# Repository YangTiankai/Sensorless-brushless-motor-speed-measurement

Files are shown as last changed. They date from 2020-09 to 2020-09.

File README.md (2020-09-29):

# Sensorless-brushless-motor-speed-measurement
使用电压比较器处理相电压的方法，测量四轴无人机无感无刷电机的转速，包含PCB和STM32源码，可以测量8路方波输入。输入端串联RC高通滤波器，可以处理有感无刷电机的霍尔传感器的转速反馈。

集成了力矩传感器的485通信模块和大疆N3飞控的通信模块。

使用了另一个项目的STM32F405核心板  
https://github.com/YangTiankai/STM32F4-Core-Board

# 系统结构

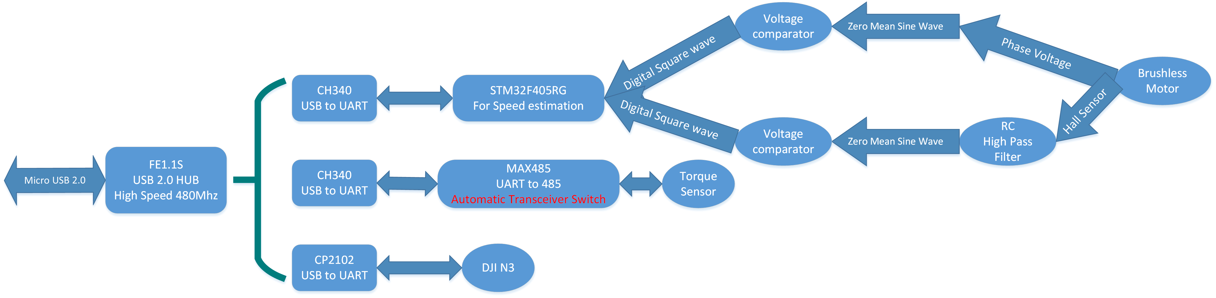
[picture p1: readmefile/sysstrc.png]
系统结构


# 测速原理
对于有12个线圈的无感电机，电机每转动一圈三相线上电压产生7个周期的正弦，将其输入电压比较器即可转化为数字方波，测量其频率可知转速。

对于有感电机，电机每转动一圈霍尔线上也是产生7个周期的正弦信号，但是该信号为恒正，使用一个10uF、10kΩ的RC高通滤波器去基频，即可得到零均正弦信号，输入电压比较器测量频率即可。

# 原理图和PCB

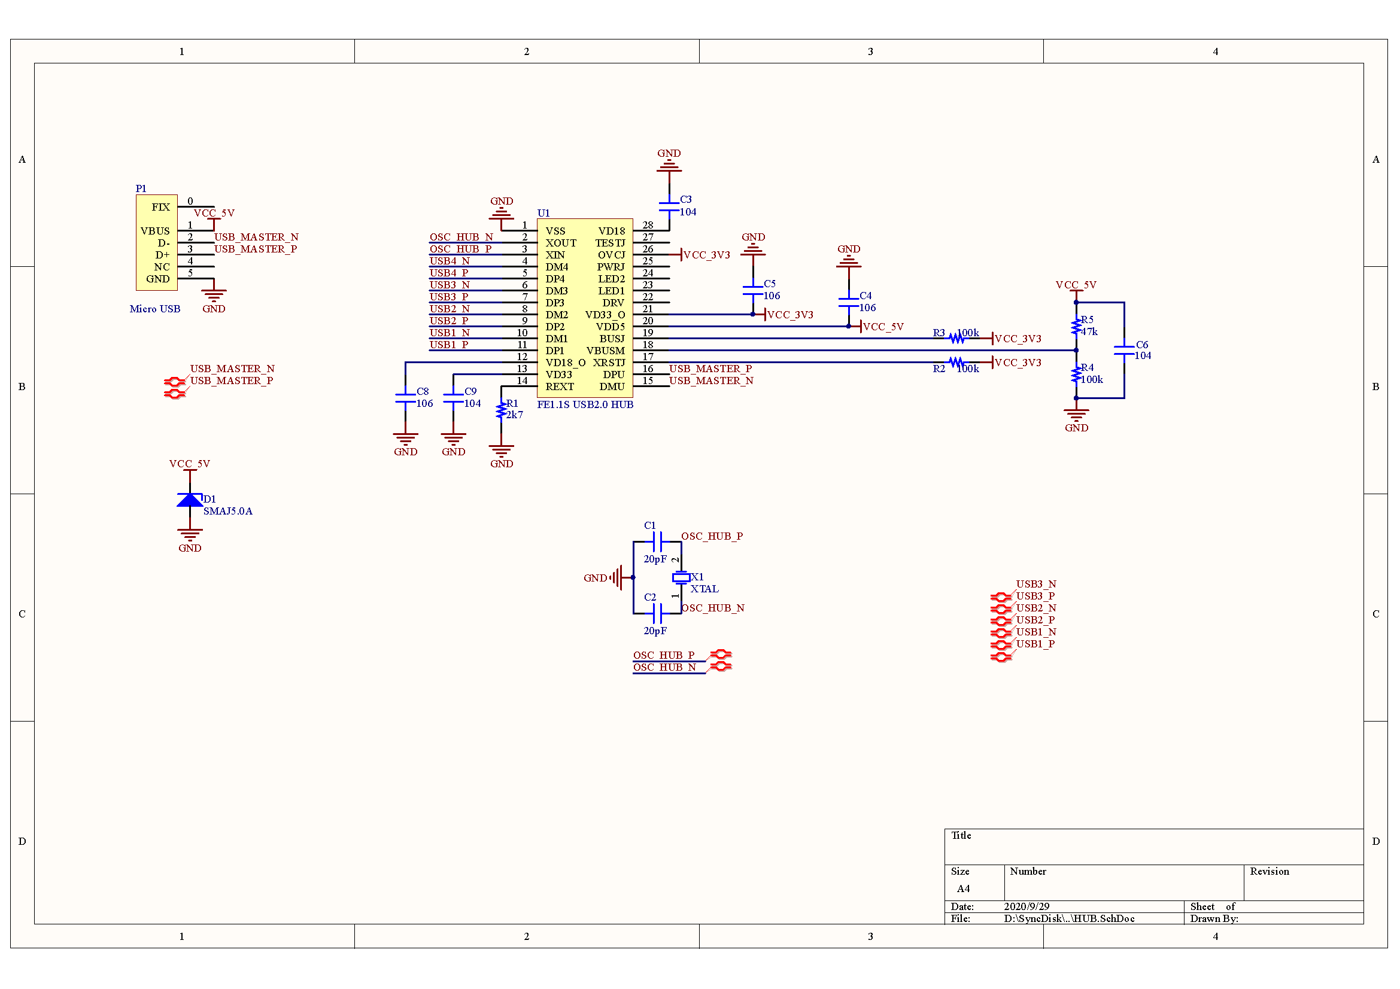
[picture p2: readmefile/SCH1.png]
SCH1


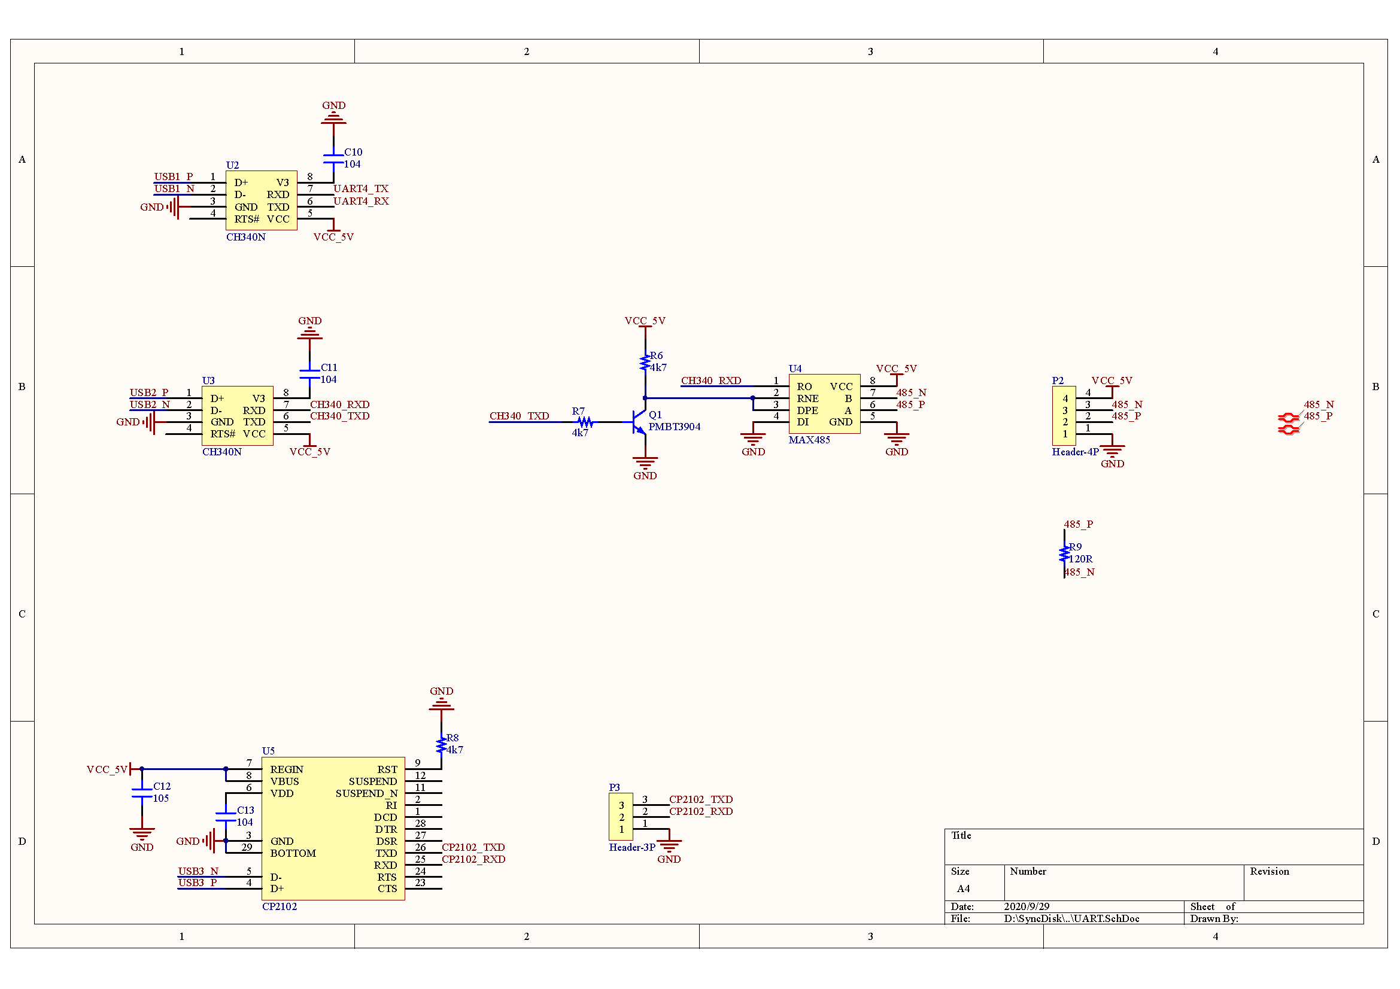
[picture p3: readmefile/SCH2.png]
SCH2


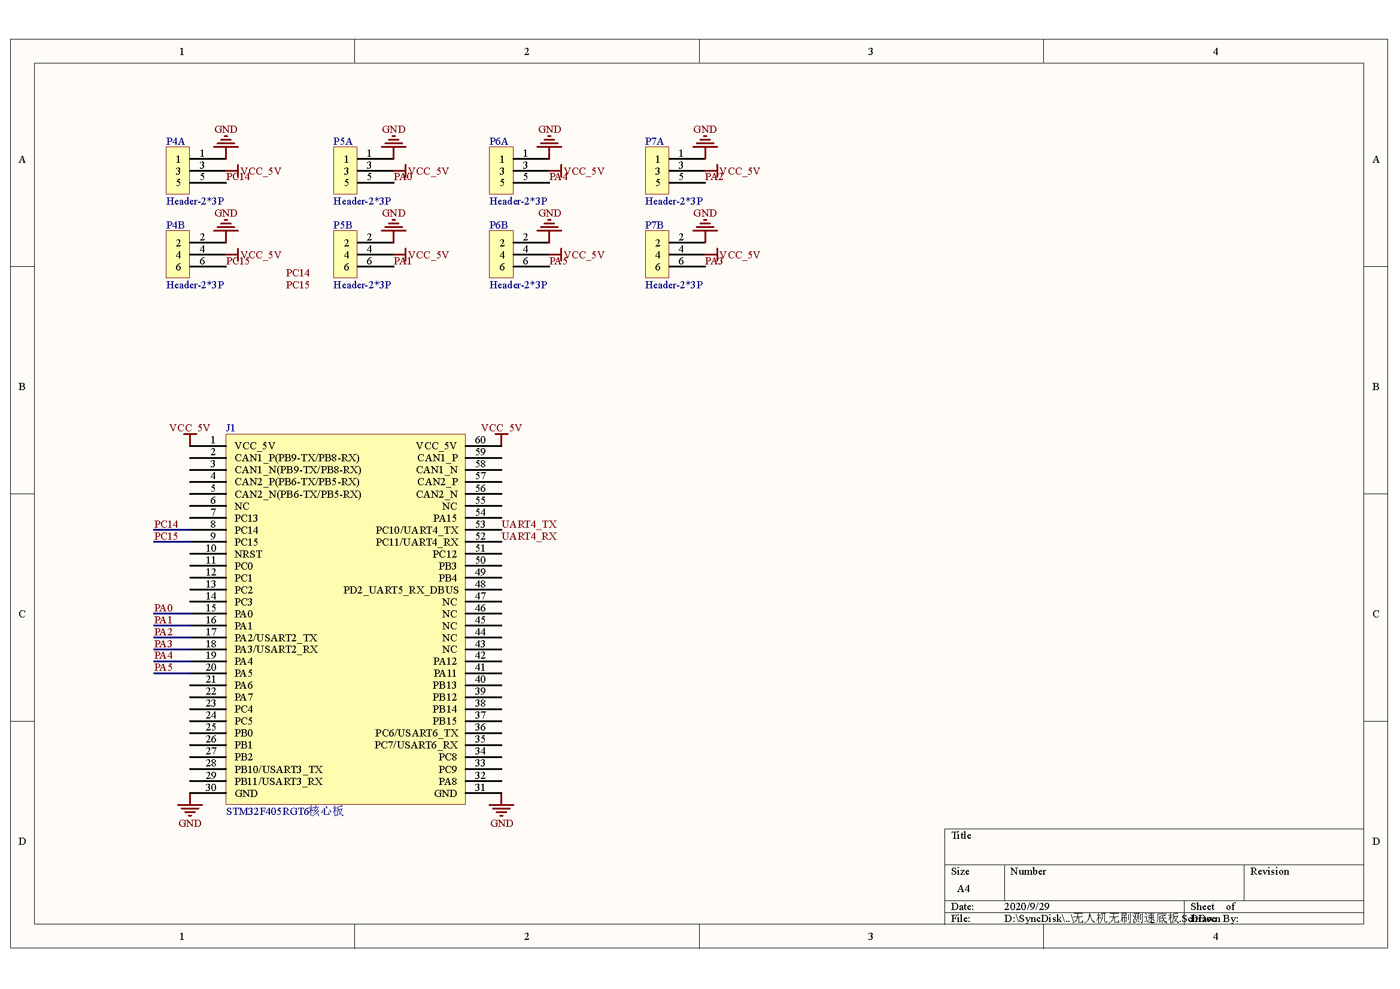
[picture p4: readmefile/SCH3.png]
SCH3


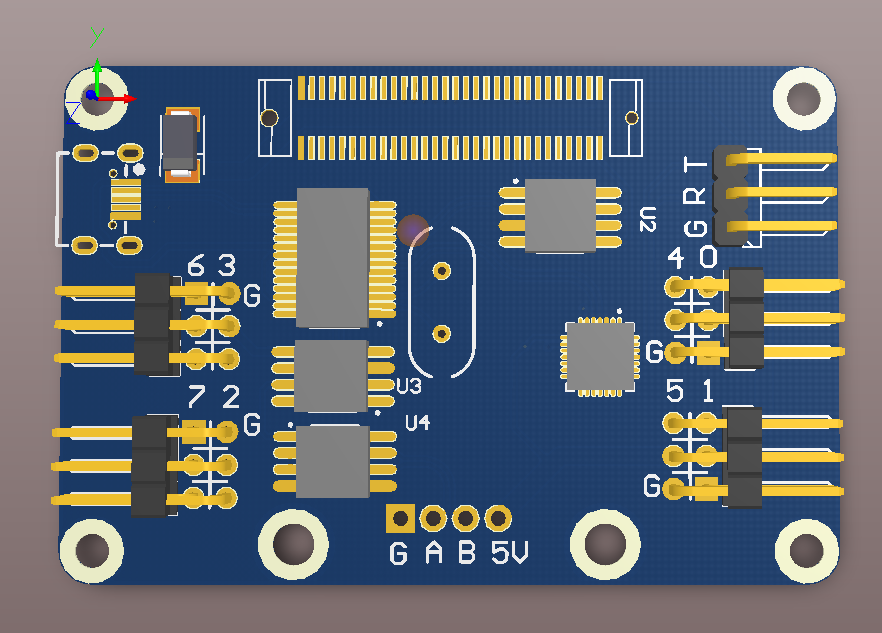
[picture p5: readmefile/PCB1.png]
PCB1


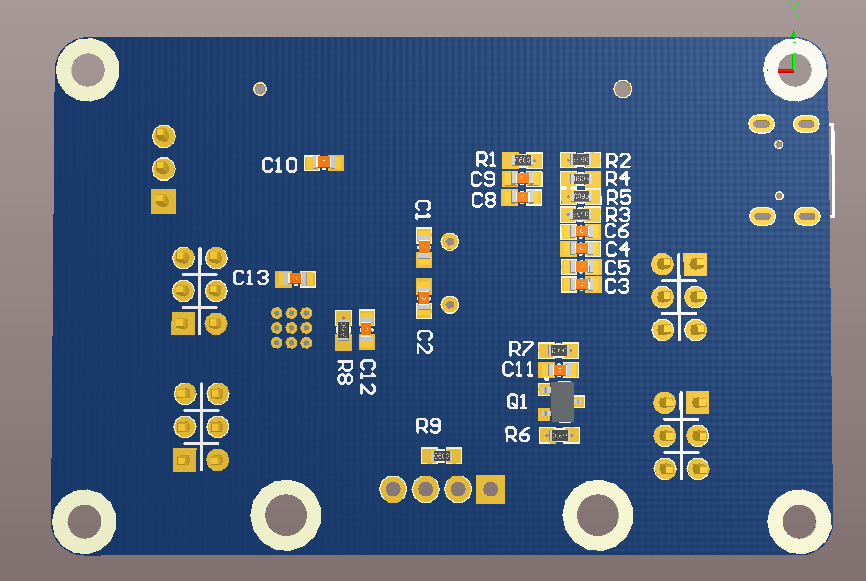
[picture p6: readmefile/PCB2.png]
PCB2


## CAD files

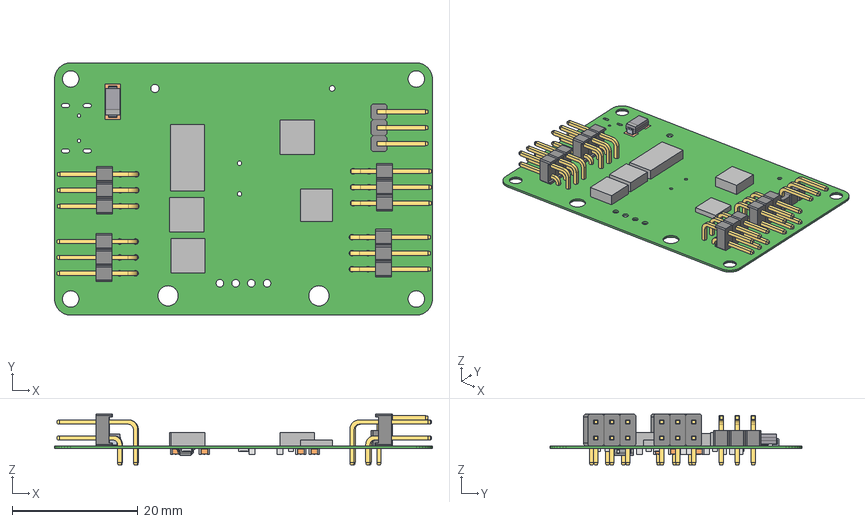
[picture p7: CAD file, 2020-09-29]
pcbfile/无人机无刷测速底板.step
60.2 x 40.2 x 8.10 mm
Board
R0603 x 9
User_Library-cap0603_cap0603_body_?? x 12
User_Library-cap0603_pad_0603_?? x 12
Extruded x 29
do214ac
do214acpad x 2
HDR-1x2_H x 12
LOGOԲ x 15
HDR2.54-1P_H x 3

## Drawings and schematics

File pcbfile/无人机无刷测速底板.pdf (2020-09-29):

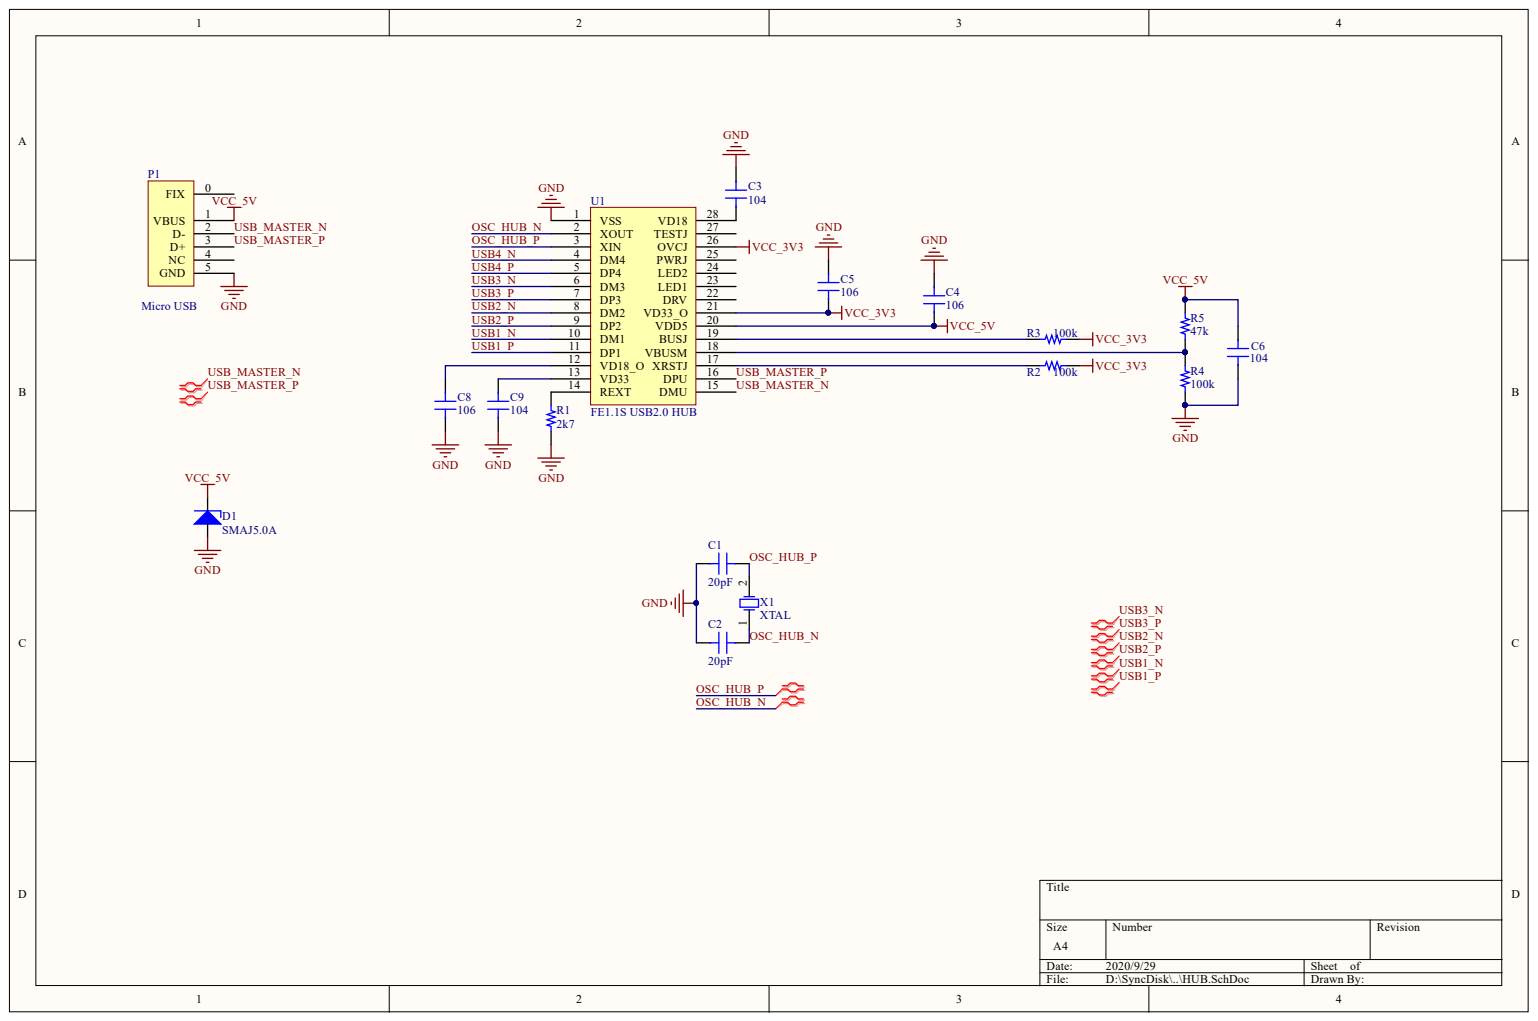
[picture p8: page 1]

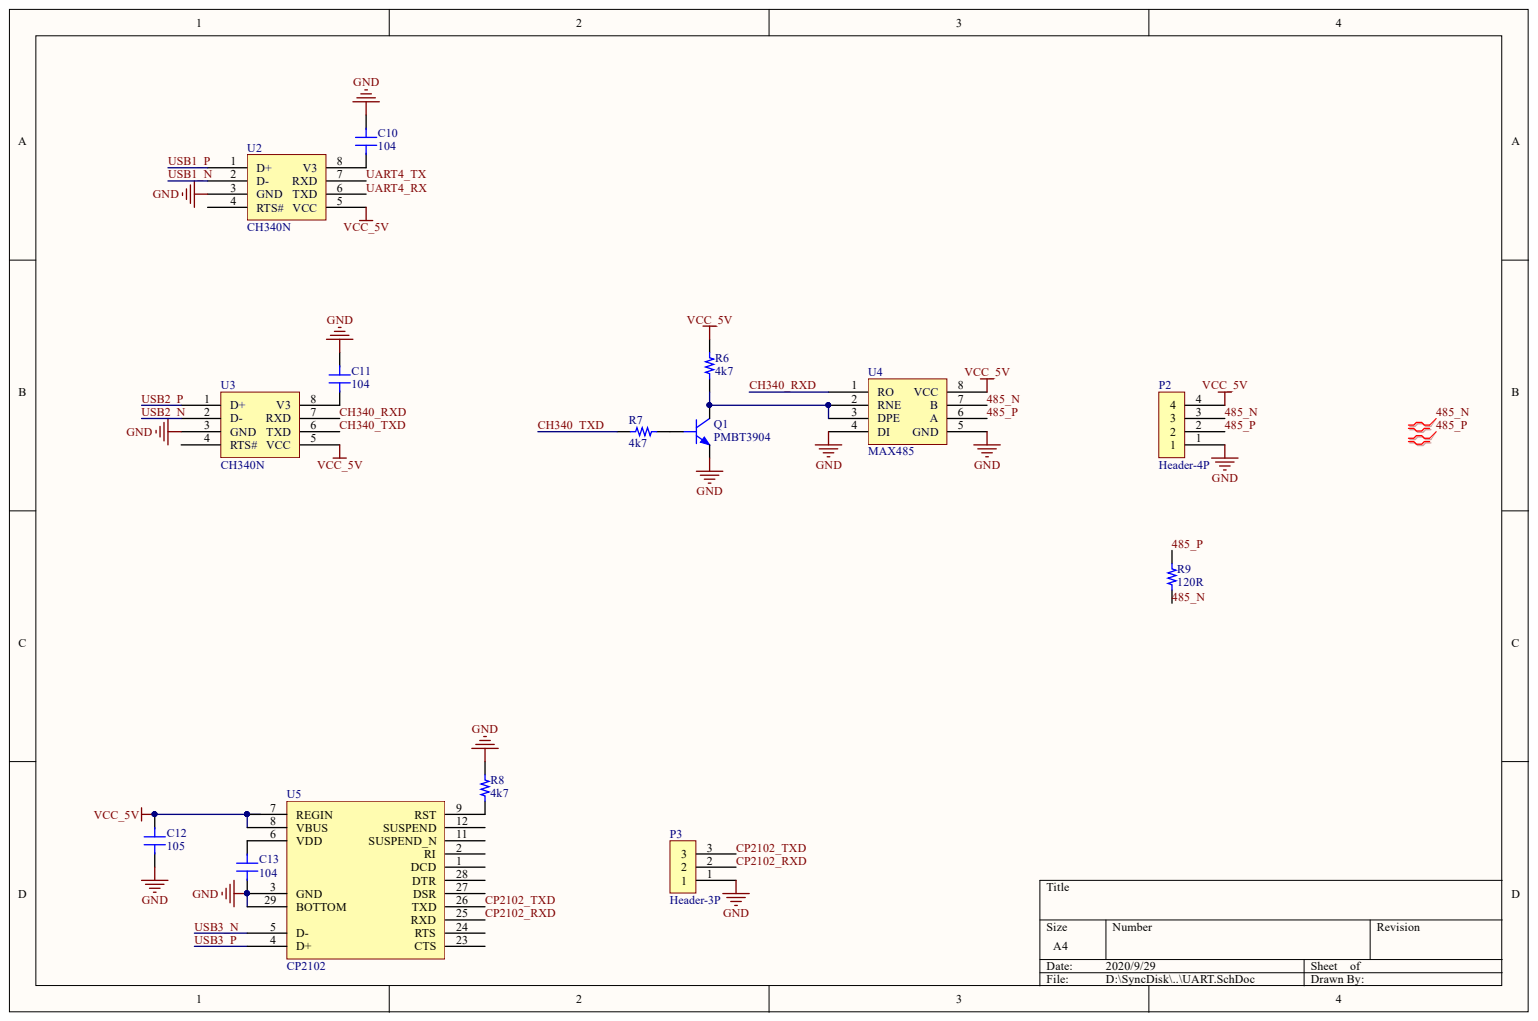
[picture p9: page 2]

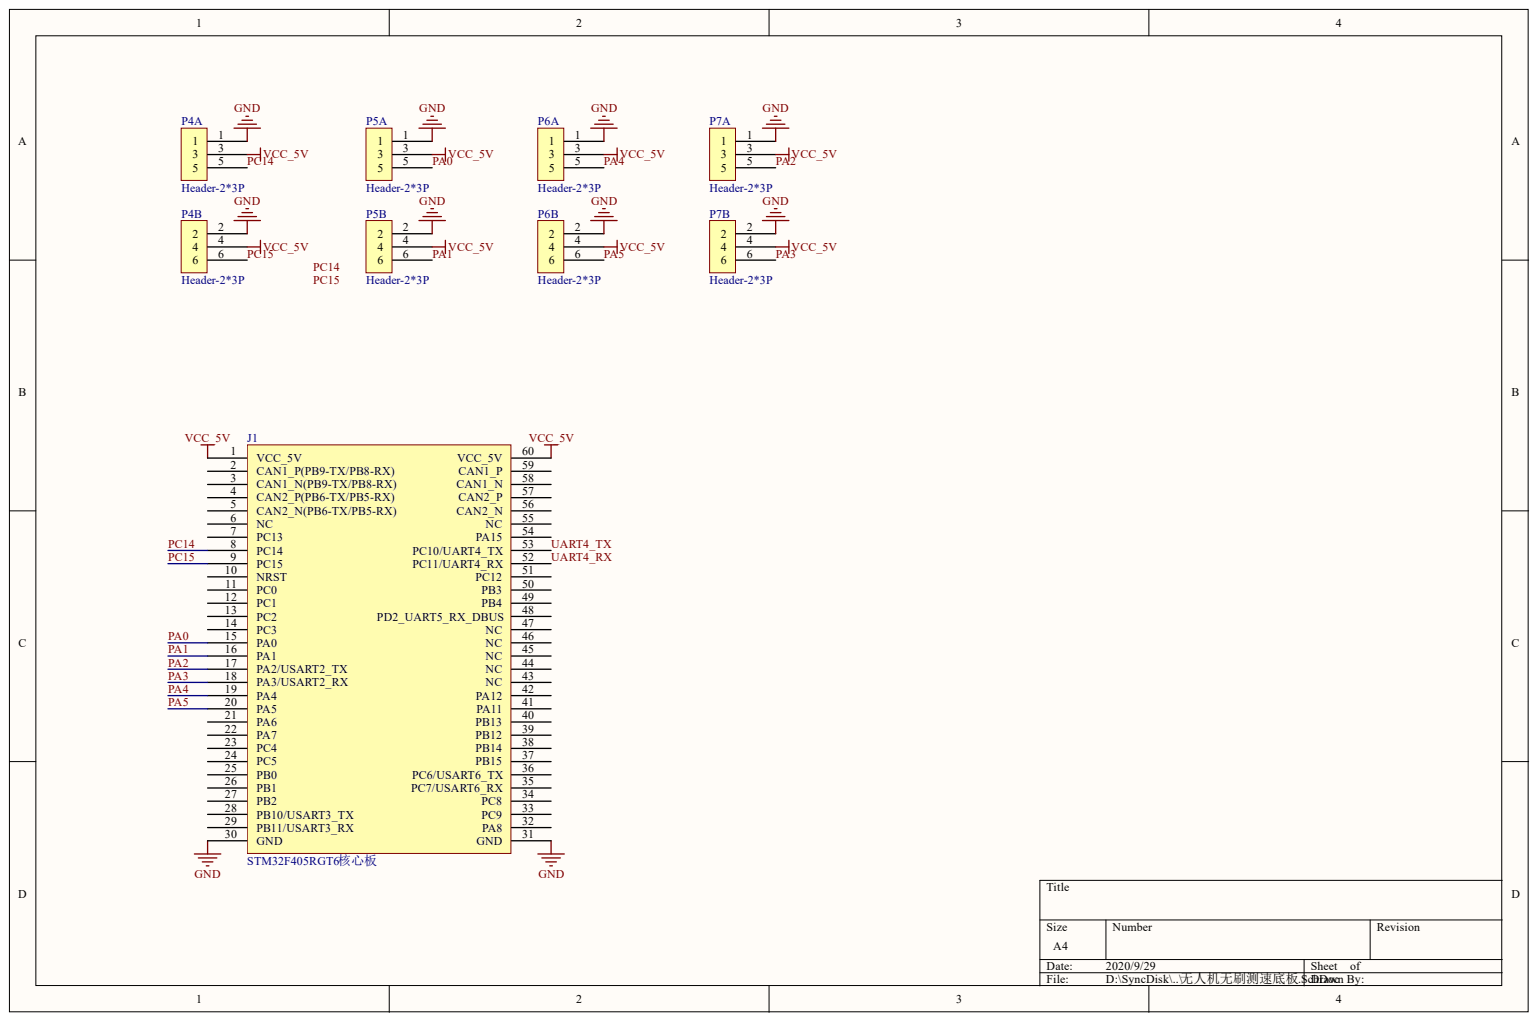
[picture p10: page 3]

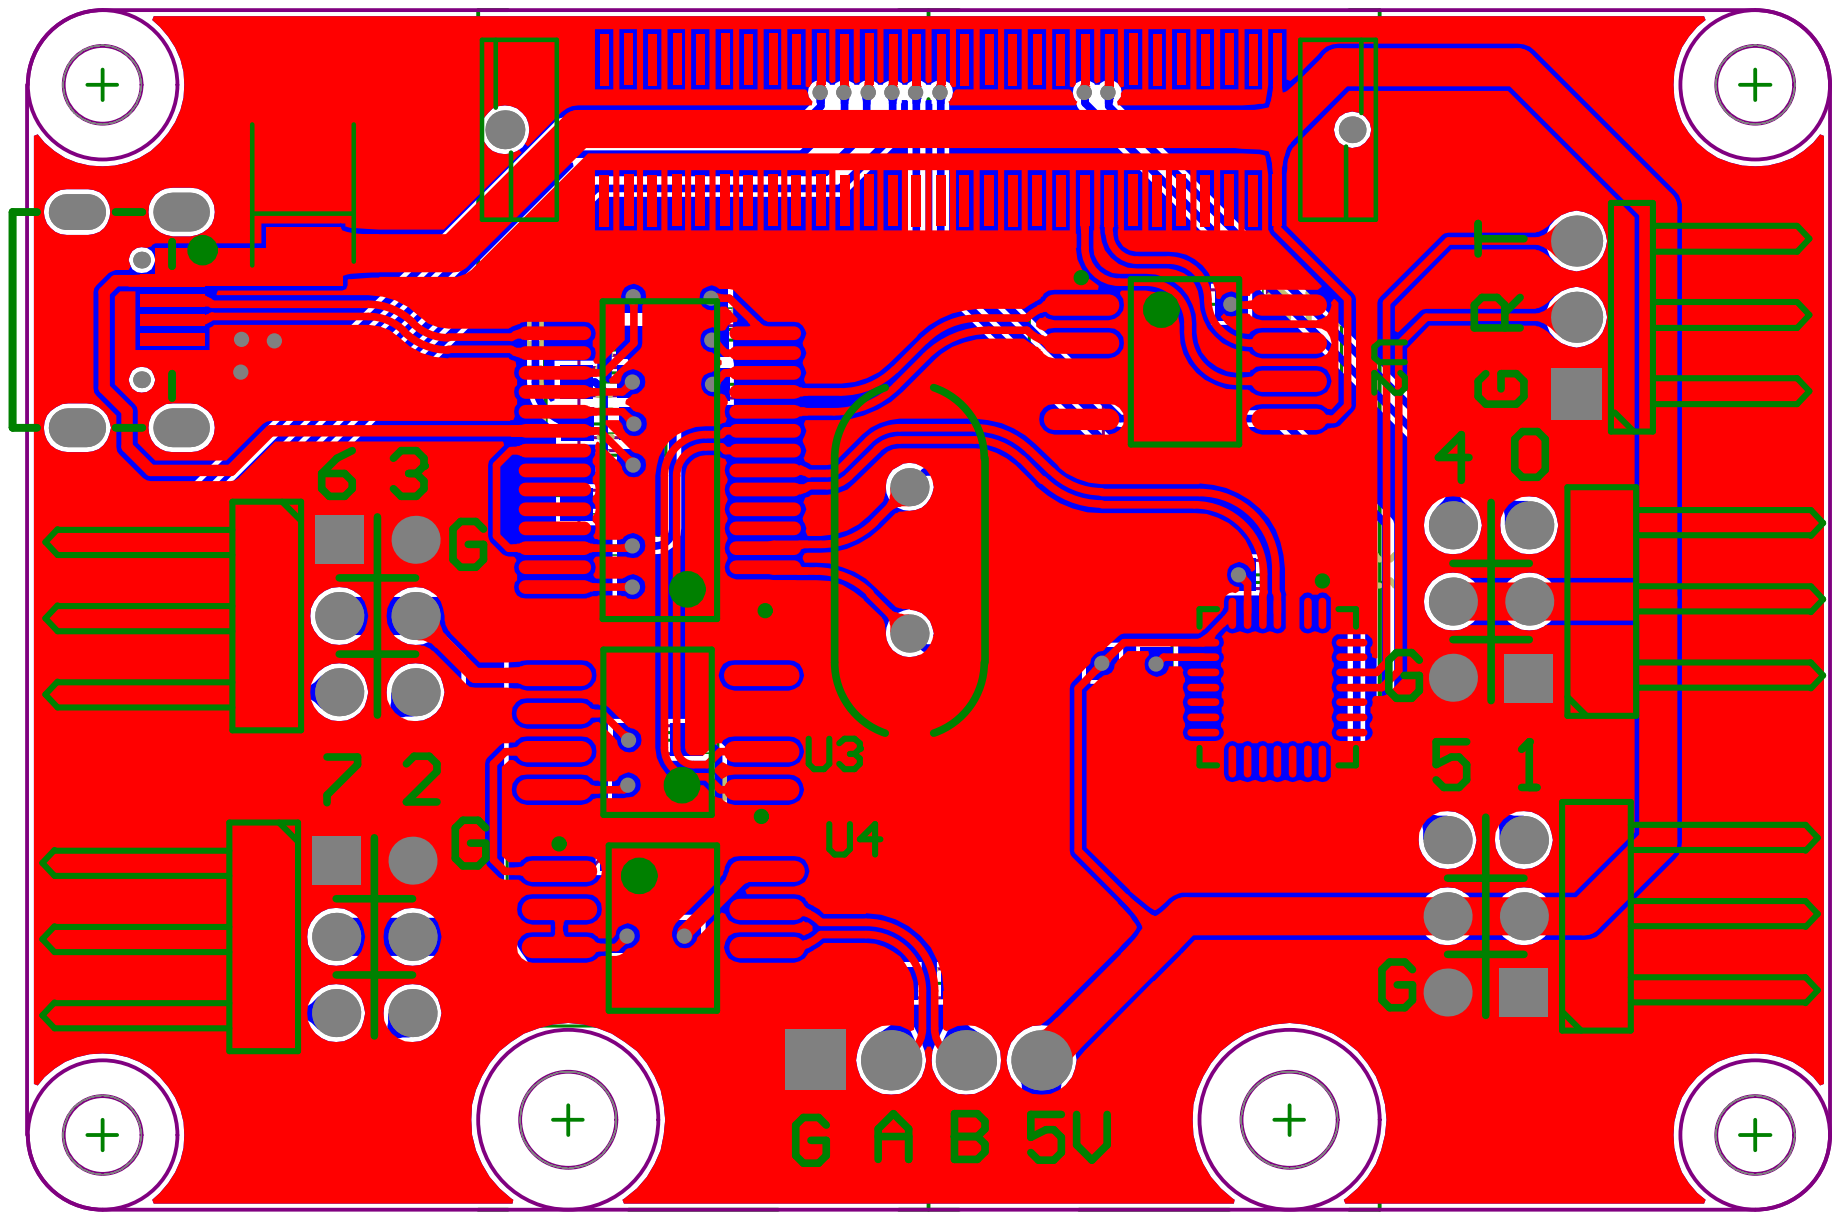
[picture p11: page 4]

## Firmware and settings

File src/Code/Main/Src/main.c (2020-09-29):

#include "main.h"
#include "math.h"



CLOCK clock = {0};
state_t state = {0};
uint8_t buff[256] = {0};
uint16_t len = 0;
uint8_t anobuff[256] = {0};
uint16_t anolen = 0;

time_stamp_t lasttime0 = {0};
time_stamp_t lasttime1 = {0};
time_stamp_t lasttime2 = {0};
time_stamp_t lasttime3 = {0};

list_t list0 = {0};
list_t list1 = {0};
list_t list2 = {0};
list_t list3 = {0};

int cnt0 = 0;
int cnt1 = 0;
int cnt2 = 0;
int cnt3 = 0;

float rpm0_10hz = 0;
float rpm1_10hz = 0;
float rpm2_10hz = 0;
float rpm3_10hz = 0;

void push_data(p_list_t plist, uint16_t data)
{
    plist->data[plist->nextout] = data;
    plist->nextout++;
    if(plist->nextout >= MAX_LIST)
    {
        plist->nextout = 0;
    }
}

float us_to_rpm(int us)
{
    return 1.0e6 * 60.0 / 7.0 / (float)us;
}

float cnt_to_rpm(int cnt)
{
    return (float)cnt * 10.0 / 7.0 * 60.0;
}

float list_avg(p_list_t plist)
{
    // int i;
    // float sum = 0;
    // for(i = 0; i <= MAX_LIST - 1; i++)
    // {
    //     sum += plist->data[i];
    // }
    // return sum / (float)MAX_LIST;


    float cur;
    int i, j;
    int length = MAX_LIST;

    float buff[MAX_LIST];
    for(i = 0; i <= MAX_LIST - 1; i++)
    {
        buff[i] = plist->data[i];
    }

    for (i = 1; i < length; i++)
    {
        cur = buff[i];    //待排序元素
        for (j = i - 1; j >= 0 && buff[j] > cur; j--)
        {
            buff[j + 1] = buff[j];
        }
        buff[j + 1] = cur;
    }

    return buff[LIST_LEFT];
}

void HAL_UART_ErrorCallback(UART_HandleTypeDef *huart)
{
    if(huart->Instance == UART4)
    {
        __HAL_UART_CLEAR_OREFLAG(&huart4);
    }   
    else if(huart->Instance == USART6)
    {
        __HAL_UART_CLEAR_OREFLAG(&huart6);
    } 
}

inline void MY_SYSCLK_Callback(void)
{
    clock.ms++;
    clock.cycle100ms++;
    clock.cyclepack++;
}

void smalldelay(void)
{
    volatile int i = 0;
    i++;
}

void HAL_GPIO_EXTI_Callback(uint16_t GPIO_Pin)
{
    if(GPIO_Pin == GPIO_PIN_0)
    {
        if( (GPIOA->IDR & (1 << 0) ) != 0 )
        {
            smalldelay();
            if( (GPIOA->IDR & (1 << 0) ) != 0 )
            {
                int cur_ms = clock.ms;
                int cur_us = TIM6->CNT;
                uint16_t data = 0;
                data = (clock.ms - lasttime0.ms) * 1000 + (cur_us - lasttime0.us);
                if(data > MIN_CYCLE_US)
                {
                    lasttime0.ms = cur_ms;
                    lasttime0.us = cur_us;
                    if( fabs( rpm0_10hz - us_to_rpm(data) ) < 10000 )
                    {
                        push_data(&list0, data);
                    }
                    cnt0++;
                }
            }
        }
    }
    else if(GPIO_Pin == GPIO_PIN_1)
    {
        if( (GPIOA->IDR & (1 << 1) ) != 0 )
        {
            smalldelay();
            if( (GPIOA->IDR & (1 << 1) ) != 0 )
            {
                int cur_ms = clock.ms;
                int cur_us = TIM6->CNT;
                uint16_t data = 0;
                data = (clock.ms - lasttime1.ms) * 1000 + (cur_us - lasttime1.us);
                if(data > MIN_CYCLE_US)
                {
                    lasttime1.ms = cur_ms;
                    lasttime1.us = cur_us;
                    if( fabs( rpm1_10hz - us_to_rpm(data) ) < 10000 )
                    {
                        push_data(&list1, data);
                    }
                    
                    cnt1++;
                }
            }
        }
    }
    else if(GPIO_Pin == GPIO_PIN_2)
    {
        if( (GPIOA->IDR & (1 << 2) ) != 0 )
        {
            smalldelay();
            if( (GPIOA->IDR & (1 << 2) ) != 0 )
            {  
                int cur_ms = clock.ms;
                int cur_us = TIM6->CNT;
                uint16_t data = 0;
                data = (clock.ms - lasttime2.ms) * 1000 + (cur_us - lasttime2.us);
                if(data > MIN_CYCLE_US)
                {
                    lasttime2.ms = cur_ms;
                    lasttime2.us = cur_us;
                    if( fabs( rpm2_10hz - us_to_rpm(data) ) < 10000 )
                    {
                        push_data(&list2, data);
                    }
                    cnt2++;
                }
            }
        }
    }
    else if(GPIO_Pin == GPIO_PIN_3)
    {
        if( (GPIOA->IDR & (1 << 3) ) != 0 )
        {
            smalldelay();
            if( (GPIOA->IDR & (1 << 3) ) != 0 )
            {
                int cur_ms = clock.ms;
                int cur_us = TIM6->CNT;
                uint16_t data = 0;
                data = (clock.ms - lasttime3.ms) * 1000 + (cur_us - lasttime3.us);
                if(data > MIN_CYCLE_US)
                {
                    lasttime3.ms = cur_ms;
                    lasttime3.us = cur_us;
                    if( fabs( rpm3_10hz - us_to_rpm(data) ) < 10000 )
                    {
                        push_data(&list3, data);
                    }
                    cnt3++;
                }
                
            }
        }
    }
}

int main(void)
{    
    HAL_Init();
    SystemClock_Config();

    LED_Core_Init();
    MX_GPIO_Init();
    MX_DMA_Init();
    MX_IWDG_Init();
    MX_USART1_UART_Init();  //核心板输出
    // MX_USART2_UART_Init();  //无线串口
    // MX_USART3_UART_Init();
    // MX_UART5_Init();        //接收机
    // MX_USART6_UART_Init();  //上位机

    MX_UART4_Init();//上位机

    MX_TIM6_Init();


    while(1)
    {
        if(clock.cycle100ms >= 100)
        {
            cycle_100ms_callback();
            clock.cycle100ms = 0;            
        }
        if(clock.cyclepack >= CYCLE_PACK_MS)
        {
            cycle_pack_callback();
            clock.cyclepack = 0;            
        }        
    }
}

float checkreal(float data, float real, float lastdata)
{
    if(real < 1000)
    {
        return 0;
    }
    else
    {
        // if(fabs(data - lastdata) < 5000)
        {
            return data;
        }
        // else
        // {
        //     return lastdata;
        // }
    }

     
    // if(fabs(data - real) > 180.0)
    // {
    //     return real;
    // }
    // else
    // {
    //     return data;
    // }
    
}


inline void cycle_pack_callback(void)
{
    static float lastrpm0 = 0;
    static float lastrpm1 = 0;
    static float lastrpm2 = 0;
    static float lastrpm3 = 0;

    uint16_t anodata[10];

    state.id = 1;
    state.cycle_ms = 10;
    state.ms = clock.ms;
    state.us = TIM6->CNT;


    float rpm0 = us_to_rpm( list_avg(&list0) );
    float rpm1 = us_to_rpm( list_avg(&list1) );
    float rpm2 = us_to_rpm( list_avg(&list2) );
    float rpm3 = us_to_rpm( list_avg(&list3) );

    

    state.pulse0 = checkreal(rpm0, rpm0_10hz, lastrpm0);
    state.pulse1 = checkreal(rpm1, rpm1_10hz, lastrpm1);
    state.pulse2 = checkreal(rpm2, rpm2_10hz, lastrpm2);
    state.pulse3 = checkreal(rpm3, rpm3_10hz, lastrpm3);

    lastrpm0 = state.pulse0;
    lastrpm1 = state.pulse1;
    lastrpm2 = state.pulse2;
    lastrpm3 = state.pulse3;


    anodata[0] = state.pulse0;
    anodata[1] = state.pulse1;
    anodata[2] = state.pulse2;
    anodata[3] = state.pulse3;

    ANOPrintS16(1, anodata, 4, anobuff, &anolen);

    // gen_state_string(&state, buff, &len);
    gen_state_pack(&state, buff, &len);

    HAL_UART_Transmit_DMA(&huart4, buff, len);
    HAL_UART_Transmit_DMA(&huart1, anobuff, anolen);
    return;
}


inline void cycle_100ms_callback(void)
{
    rpm0_10hz = cnt_to_rpm(cnt0);
    rpm1_10hz = cnt_to_rpm(cnt1);
    rpm2_10hz = cnt_to_rpm(cnt2);
    rpm3_10hz = cnt_to_rpm(cnt3);

    cnt0 = 0;
    cnt1 = 0;
    cnt2 = 0;
    cnt3 = 0;

    LED_Core_Turn();
    HAL_IWDG_Refresh(&hiwdg);
    return;
}
